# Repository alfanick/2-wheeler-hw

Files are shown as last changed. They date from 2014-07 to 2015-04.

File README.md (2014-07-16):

# TwoWheeler
TwoWheeler is Self Balancing Robot implemented using [XMOS startKIT](http://www.xmos.com/startkit) platform.

The robot is solving physical problem of inverted pendulum using PID regulator connecting motors with accelerometer. However its hardware design has much more features:
* 8 core 32-bit microcontroller
* bluetooth transceiver
* two distance meters
* motor driver with current sensing
* buck converter designed for use with LiPo battery
* battery voltage monitoring
* Over-The-Air parameters programming to built-in flash
* high torque motors with encoders

## Parts

* XMOS firmware - more in [balancer README](sw_twowheeler/app_balancer/README.md)
* computer app - API available in Ruby and console command interface with scripting (more in [documentation](ruby_twowheeler/README.md))
* circuit schematic and PCB design
* hardware design - not yet documented

## Authors

* Amadeusz Juskowiak - amadeusz@me.com
* Piotr Żurkowski  - kareth92@gmail.com

Inspired by Embedded Systems course at Poznan University of
Technology.

## License

*Copyright 2014 Amadeusz Juskowiak*

Licensed under the Apache License, Version 2.0 (the "License");
you may not use this file except in compliance with the License.
You may obtain a copy of the License at http://www.apache.org/licenses/LICENSE-2.0

Unless required by applicable law or agreed to in writing, software
distributed under the License is distributed on an "AS IS" BASIS,
WITHOUT WARRANTIES OR CONDITIONS OF ANY KIND, either express or implied.
See the License for the specific language governing permissions and
limitations under the License.

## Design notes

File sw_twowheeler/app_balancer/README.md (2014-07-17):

# TwoWheeler

## Commands

This is glossary of commands accepted and returned by TwoWheeler.
Every command must be ended with carriage return character to be
read.

### Requests

| Command | Description |
| --- | --- |
| FLASH | next cmd will use flash memory |
| FLASH=k | next k-cmds will use flash |
| V? | get battery voltage |
| PID? | get current PID coefficients |
| PID=p,i,d | set PID coefficients |
| PIDLP? | get current PID lowpass coeff  |
| PIDLP=a | set PID lowpass coefficient |
| RPM? | get RPM of motors |
| T? | get target angle |
| T=a | set target angle |
| T | set current angle as target |
| A? | get current pitch angle |
| ALP? | get current low pass coeff |
| ALP=a | set angle low pass coefficient |
| C? | get motors current |
| S | starts balancing |
| X | stop balancing |
| VER? | get firmware version |
| LOOPTIME? | get last loop execution time |
| LOOPDELAY?  | get loop delay |
| LOOPDELAY=t | set loop delay |
| SB? | get speed boost |
| SB=a | set speed boost |
| ST? | get speed threshold |
| ST=a | set speed threshold |

#### FLASH command

Lorem ipsum

### Replies

| Command | Description |
| --- | --- |
| OK | default command acknowledge |
| ERROR | malformed command |
| V=n | battery voltage in mV |
| PID=p,i,d | current PID coefficients |
| PIDLP=a | current PID lowpass coefficient|
| RPM=l,r | current motor RPM |
| C=l,r | motors current |
| T=a | current target angle |
| A=a | current pitch angle |
| ALP=a | current angle low pass coeff |
| VER=v | firmware git commit id |
| LOOPTIME=v  | last loop execution time in ms |
| LOOPDELAY=t | current loop delay in ms |
| SB=a | current speed boost |
| ST=a | current speed threshold |

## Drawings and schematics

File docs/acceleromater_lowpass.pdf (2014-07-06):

## Implemented on XMOS (angle lowpass=0.02, vector median=3)

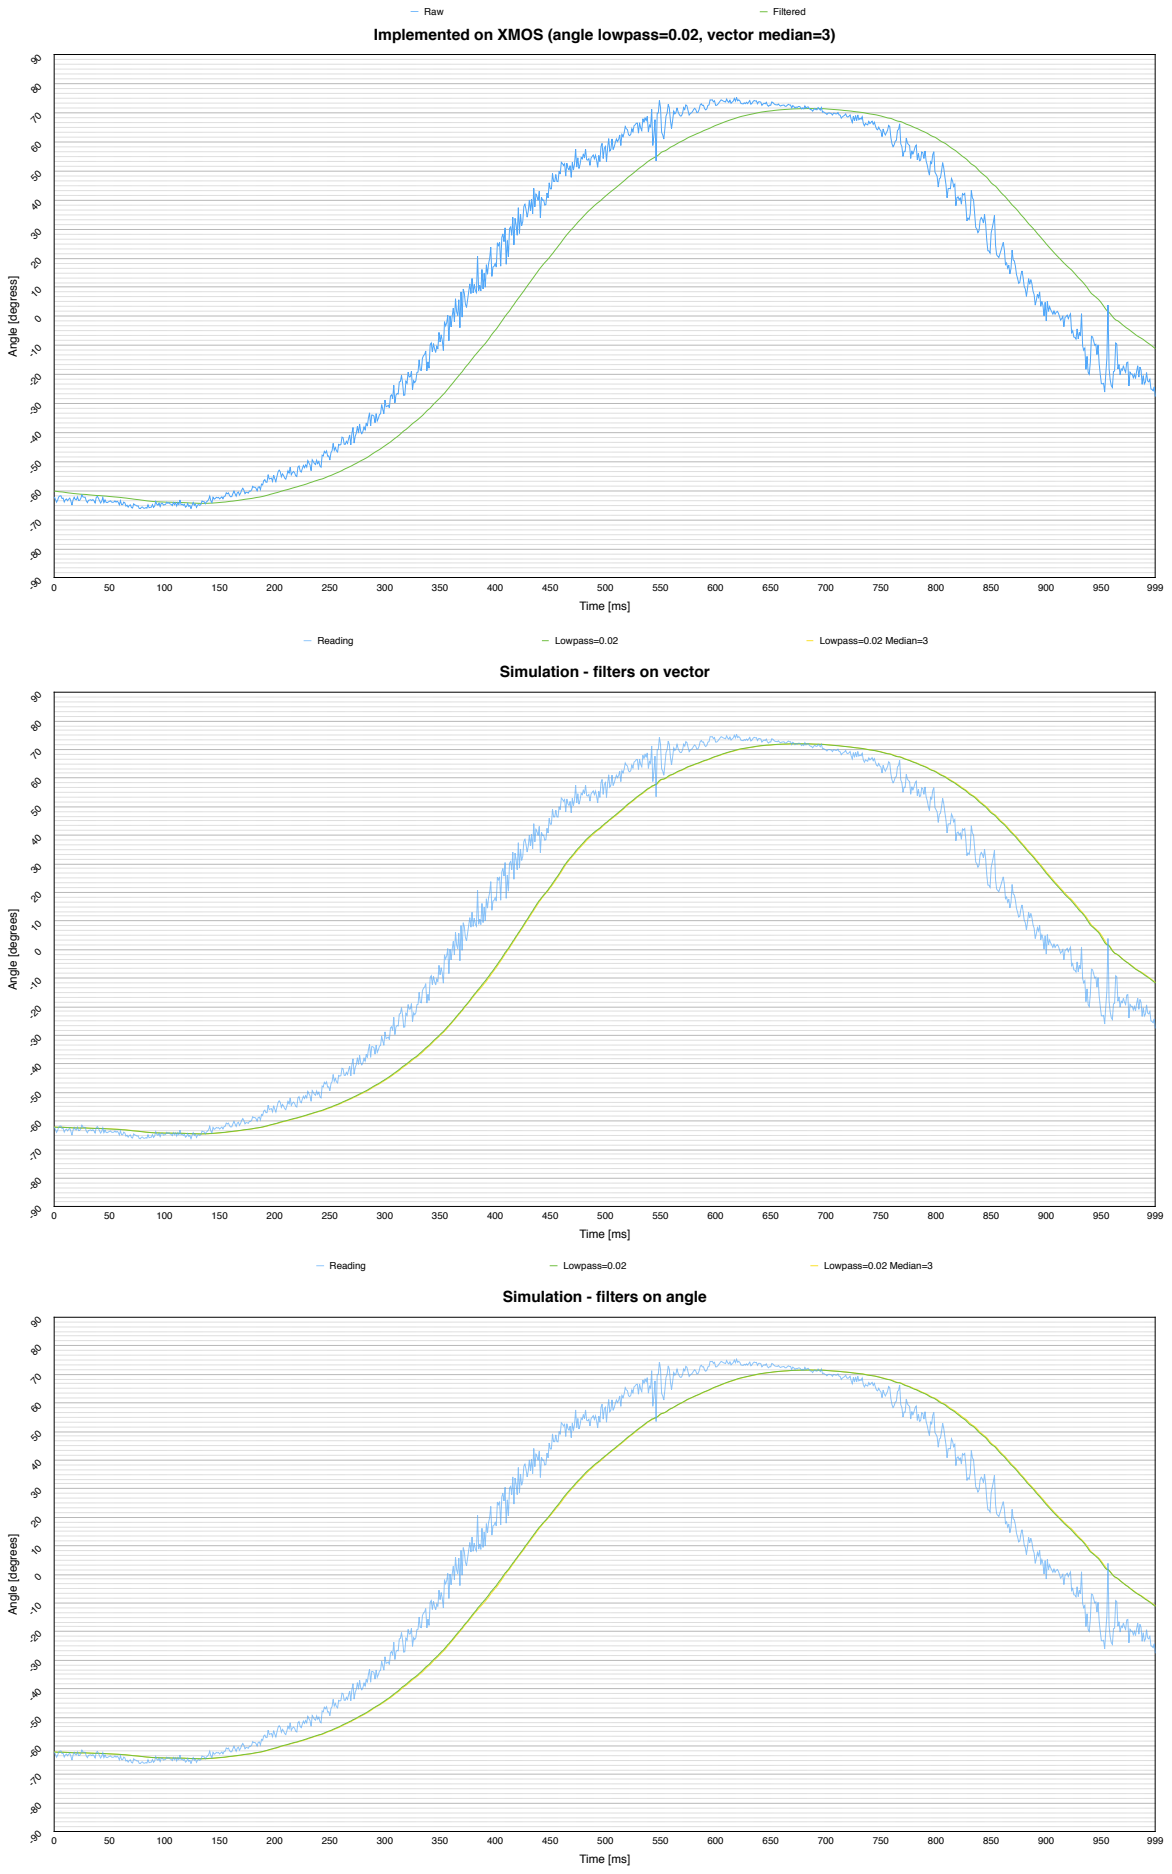
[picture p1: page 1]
Angle [degrees]; Time [ms]; Reading; Lowpass=0.02; Lowpass=0.02 Median=3; Angle [degress]; Raw; Filtered

Simulation - filters on vector

Simulation - filters on angle

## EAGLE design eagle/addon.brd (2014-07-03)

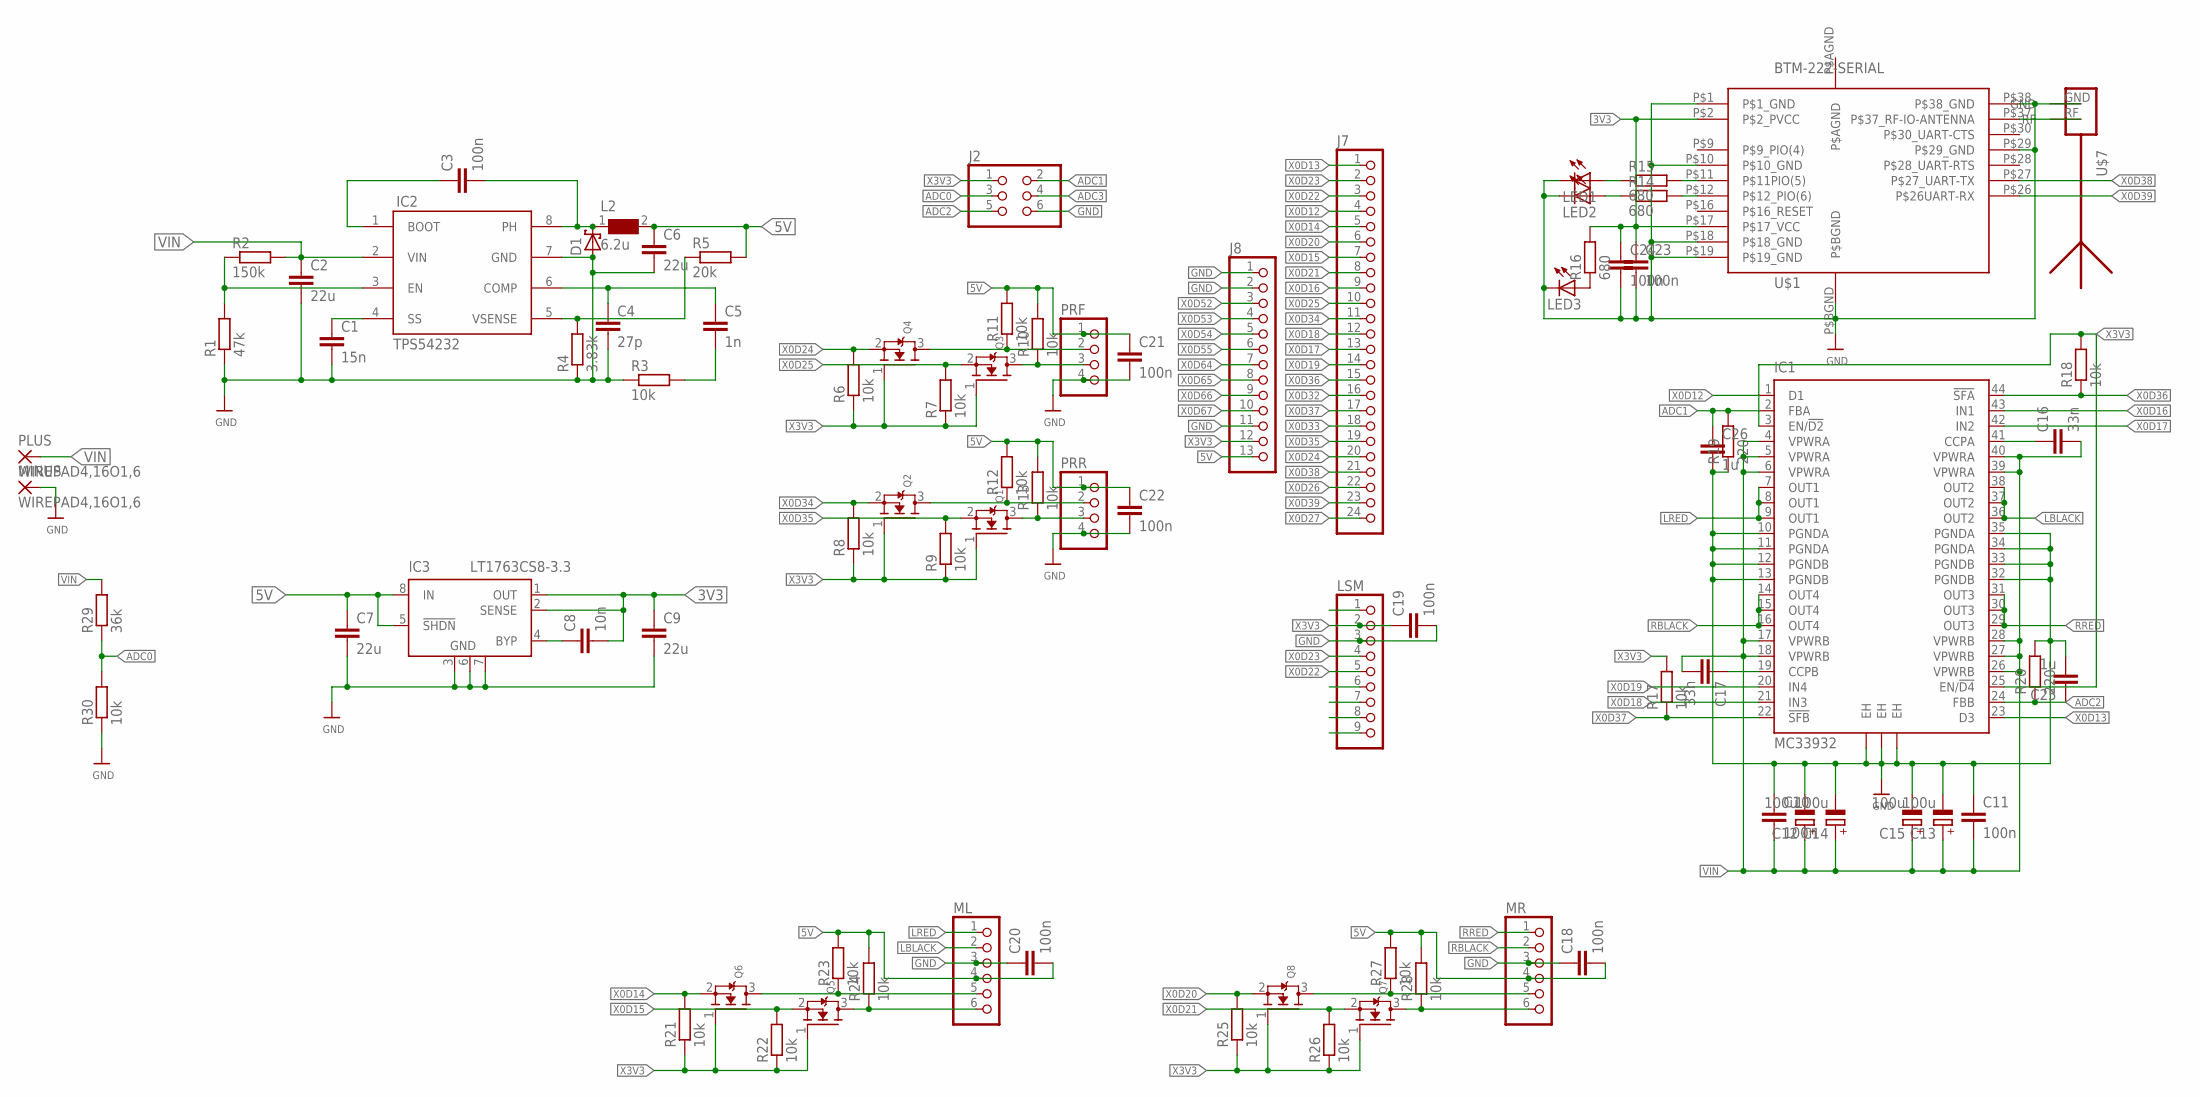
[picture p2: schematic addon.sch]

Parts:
C1: 15n; C0603
C2: 22u; C1210
C3, C10, C11, C18, C19, C20, C21, C22, C23, C24: 100n; C0603
C4: 27p; C0603
C5: 1n; C0603
C6: 22u; C1206
C7, C9: 22u; C0603
C8: 10n; C0603
C12, C13, C14, C15: 100u; D/7343-31R
C16, C17: 33n; C0603
C25, C26: 1u; C0603
D1: SCHOTTKY-DIODESMD; SMB
IC1: MC33932; HSOP44
IC2: TPS54232; YOURITRONICS_SO8
IC3: LT1763CS8-3.3; SOIC8
J2: PINHD-2X3; 2X03
J7: PINHD-1X24; 1X24
J8: PINHD-1X13; 1X13
L2: 6.2u; EAGLELIBRARY_WUERTH_ELEKTRONIK_EISOS_VERSION_6_WE-TPC_6823
LED1, LED2, LED3: LEDCHIPLED_0603; CHIPLED_0603
LSM: PINHD-1X9; 1X09
MINUS: WIREPAD4,16O1,6; 4,16O1,6
ML: PINHD-1X6; 1X06
MR: PINHD-1X6; 1X06
PLUS: WIREPAD4,16O1,6; 4,16O1,6
PRF: PINHD-1X4; 1X04
PRR: PINHD-1X4; 1X04
Q1, Q2, Q3, Q4, Q5, Q6, Q7, Q8: MOSFET-NREFLOW; SOT23-R
R1: 47k; R0603
R2: 150k; R0603
R3, R6, R7, R8, R9, R10, R11, R12, R13, R17, R18, R21, R22, R23, R24, R25, R26, R27, R28, R30: 10k; R0603
R4: 3.83k; R0603
R5: 20k; R0603
R14, R15, R16: 680; R0603
R19, R20: 220; R0603
R29: 36k; R0603
U$1: BTM-222-SERIAL; BTM-222
U$7: ANTENNA_1RIGHT; SWRA117D_RIGHT

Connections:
3V3: C8.2, C9.1, C23.1, C24.1, IC3.1 (OUT), IC3.2 (SENSE), R16.2, U$1.P$2 (P$2_PVCC), U$1.P$17 (P$17_VCC)
5V: C6.1, C7.1, C18.2, C20.2, C21.1, C22.1, IC3.5 (!SHDN), IC3.8 (IN), J8.13, L2.2, ML.4, MR.4, PRF.1, PRR.1, R5.2, R10.2, R11.2, R12.2, R13.2, R23.2, R24.2, R27.2, R28.2
ADC0: J2.3, R29.1, R30.2
ADC1: C26.1, IC1.2 (FBA), J2.2, R19.2
ADC2: C25.1, IC1.24 (FBB), J2.5, R20.1
ADC3: J2.4
GND: C1.2, C2.2, C4.2, C6.2, C7.2, C9.2, C10.1, C11.1, C12.-, C13.-, C14.-, C15.-, C18.1, C19.2, C20.1, C21.2, C22.2, C23.2, C24.2, C25.2, C26.2, D1.A, IC1.10 (PGNDA), IC1.11 (PGNDA), IC1.12 (PGNDB), IC1.13 (PGNDB), IC1.32 (PGNDB), IC1.33 (PGNDB), IC1.34 (PGNDA), IC1.35 (PGNDA), IC1.EH@1 (EH), IC1.EH@2 (EH), IC1.EH@3 (EH), IC2.7 (GND), IC3.3 (GND), IC3.6 (GND), IC3.7 (GND), J2.6, J8.1, J8.2, J8.11, LED1.C, LED2.C, LED3.C, LSM.3, MINUS.1, ML.3, MR.3, PRF.4, PRR.4, R1.1, R3.1, R4.1, R19.1, R20.2, R30.1, U$1.P$1 (P$1_GND), U$1.P$10 (P$10_GND), U$1.P$18 (P$18_GND), U$1.P$19 (P$19_GND), U$1.P$29 (P$29_GND), U$1.P$38 (P$38_GND), U$1.P$BGND, U$7.GND
LBLACK: IC1.36 (OUT2), IC1.37 (OUT2), IC1.38 (OUT2), ML.2
LRED: IC1.7 (OUT1), IC1.8 (OUT1), IC1.9 (OUT1), ML.1
unnamed: IC2.3 (EN), R1.2, R2.1
unnamed: C8.1, IC3.4 (BYP)
unnamed: PRR.3, Q1.3 (D), R13.1
unnamed: C3.1, IC2.1 (BOOT)
unnamed: C3.2, D1.C, IC2.8 (PH), L2.1
unnamed: C1.1, IC2.4 (SS)
unnamed: PRR.2, Q2.3 (D), R12.1
unnamed: C4.1, C5.1, IC2.6 (COMP)
unnamed: PRF.3, Q3.3 (D), R10.1
unnamed: C5.2, R3.2
unnamed: IC2.5 (VSENSE), R4.2, R5.1
unnamed: PRF.2, Q4.3 (D), R11.1
unnamed: U$1.P$37 (P$37_RF-IO-ANTENNA), U$7.RF
unnamed: R15.2, U$1.P$11 (P$11PIO(5))
unnamed: R14.2, U$1.P$12 (P$12_PIO(6))
unnamed: LED1.A, R15.1
unnamed: LED2.A, R14.1
unnamed: LED3.A, R16.1
unnamed: C16.1, IC1.41 (CCPA)
unnamed: C17.1, IC1.19 (CCPB)
unnamed: ML.6, Q5.3 (D), R24.1
unnamed: ML.5, Q6.3 (D), R23.1
unnamed: MR.6, Q7.3 (D), R28.1
unnamed: MR.5, Q8.3 (D), R27.1
P$AGND: U$1.P$AGND
RBLACK: IC1.14 (OUT4), IC1.15 (OUT4), IC1.16 (OUT4), MR.2
RRED: IC1.29 (OUT3), IC1.30 (OUT3), IC1.31 (OUT3), MR.1
VIN: C2.1, C10.2, C11.2, C12.+, C13.+, C14.+, C15.+, C16.2, C17.2, IC1.4 (VPWRA), IC1.5 (VPWRA), IC1.6 (VPWRA), IC1.17 (VPWRB), IC1.18 (VPWRB), IC1.26 (VPWRB), IC1.27 (VPWRB), IC1.28 (VPWRB), IC1.39 (VPWRA), IC1.40 (VPWRA), IC2.2 (VIN), PLUS.1, R2.2, R29.2
X0D12: IC1.1 (D1), J7.4
X0D13: IC1.23 (D3), J7.1
X0D14: J7.5, Q6.2 (S), R21.2
X0D15: J7.7, Q5.2 (S), R22.2
X0D16: IC1.43 (IN1), J7.9
X0D17: IC1.42 (IN2), J7.13
X0D18: IC1.21 (IN3), J7.12
X0D19: IC1.20 (IN4), J7.14
X0D20: J7.6, Q8.2 (S), R25.2
X0D21: J7.8, Q7.2 (S), R26.2
X0D22: J7.3, LSM.5
X0D23: J7.2, LSM.4
X0D24: J7.20, Q4.2 (S), R6.2
X0D25: J7.10, Q3.2 (S), R7.2
X0D26: J7.22
X0D27: J7.24
X0D32: J7.16
X0D33: J7.18
X0D34: J7.11, Q2.2 (S), R8.2
X0D35: J7.19, Q1.2 (S), R9.2
X0D36: IC1.44 (!SFA), J7.15, R18.1
X0D37: IC1.22 (!SFB), J7.17, R17.1
X0D38: J7.21, U$1.P$27 (P$27_UART-TX)
X0D39: J7.23, U$1.P$26 (P$26UART-RX)
X0D52: J8.3
X0D53: J8.4
X0D54: J8.5
X0D55: J8.6
X0D64: J8.7
X0D65: J8.8
X0D66: J8.9
X0D67: J8.10
X3V3: C19.1, IC1.3 (EN/!D2), IC1.25 (EN/!D4), J2.1, J8.12, LSM.2, Q1.1 (G), Q2.1 (G), Q3.1 (G), Q4.1 (G), Q5.1 (G), Q6.1 (G), Q7.1 (G), Q8.1 (G), R6.1, R7.1, R8.1, R9.1, R17.2, R18.2, R21.1, R22.1, R25.1, R26.1

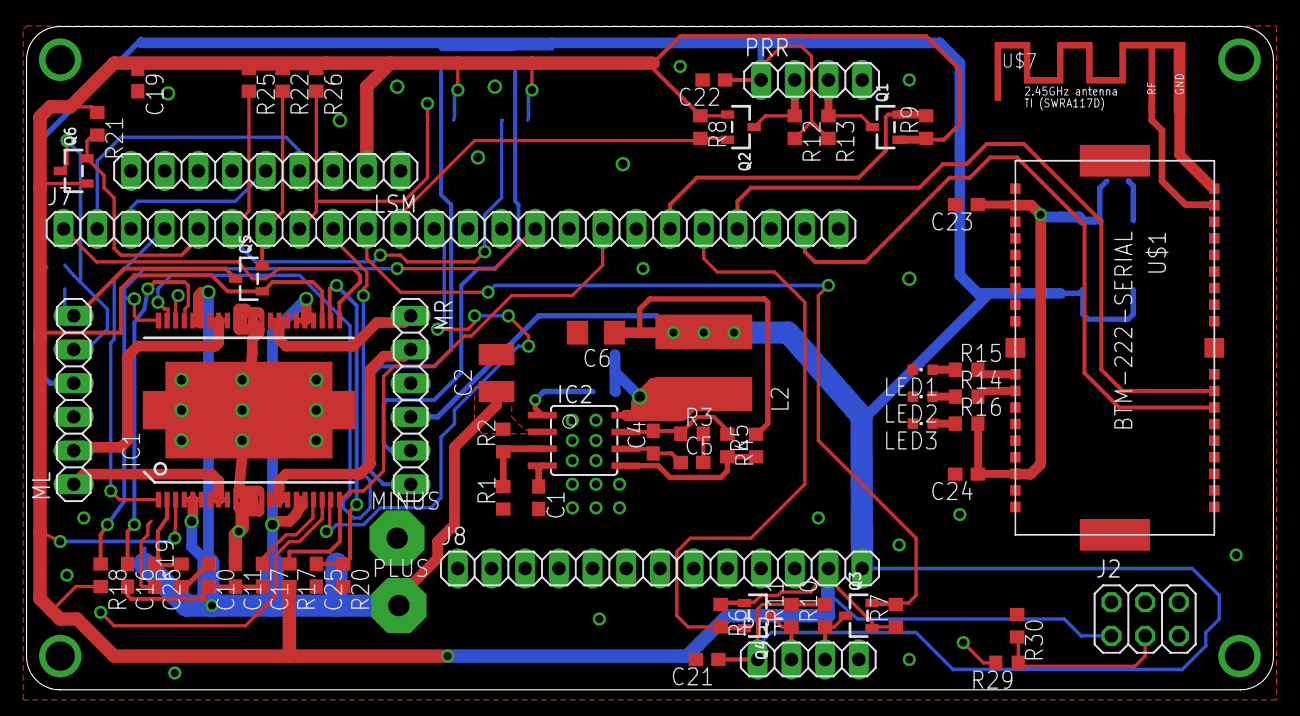
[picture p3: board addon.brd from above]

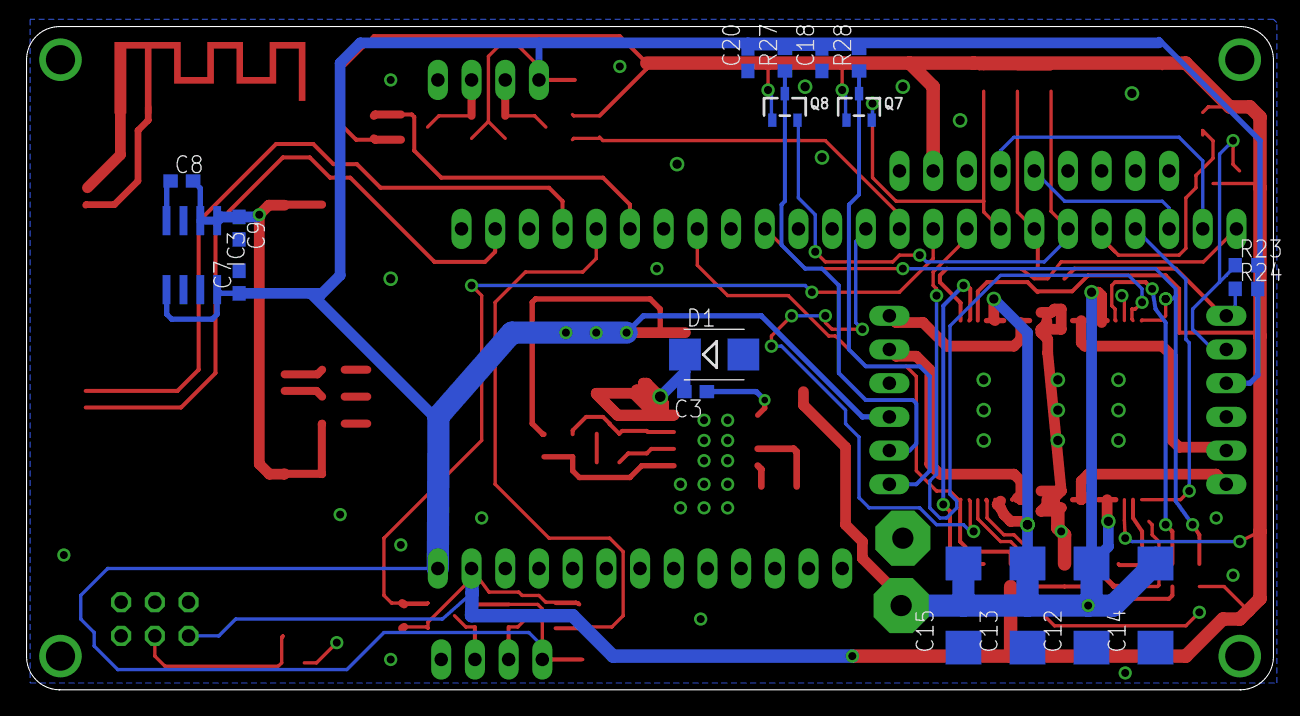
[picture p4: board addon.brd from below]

Board: 2 copper layers, 94.0 x 50.0 mm, 84 parts (18 on the bottom side), 56 nets.

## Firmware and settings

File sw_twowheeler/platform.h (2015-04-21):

#ifndef TWO_WHEELER_PLATFORM_H_
#define TWO_WHEELER_PLATFORM_H_

#define   FRONT_DISTANCE_SENSOR_TRIGGER            XS1_PORT_1I
#define      FRONT_DISTANCE_SENSOR_ECHO            XS1_PORT_1J

#define    REAR_DISTANCE_SENSOR_TRIGGER            XS1_PORT_1K
#define       REAR_DISTANCE_SENSOR_ECHO            XS1_PORT_1L

#define             MOTION_SENSOR_CLOCK            XS1_PORT_1G
#define              MOTION_SENSOR_DATA            XS1_PORT_1H

#define              BLUETOOTH_TRANSMIT            XS1_PORT_1P
#define               BLUETOOTH_RECEIVE            XS1_PORT_1O

#define              LEFT_MOTOR_DISABLE            XS1_PORT_1E
#define               LEFT_MOTOR_STATUS            XS1_PORT_1M

#define             RIGHT_MOTOR_DISABLE            XS1_PORT_1F
#define              RIGHT_MOTOR_STATUS            XS1_PORT_1N

#define               MOTORS_DIRECTIONS            XS1_PORT_4D
#define                  MOTORS_SENSORS            XS1_PORT_4C

#include <platform.h>
#include <xs1.h>

#include <uart_fast_tx.h>
#include <uart_fast_rx.h>
#include <distance_sensor.h>
#include <imu10.h>
#include <motors.h>

distance_sensor_t distance_sensors[2] = {
  { FRONT_DISTANCE_SENSOR_TRIGGER, FRONT_DISTANCE_SENSOR_ECHO },
  {  REAR_DISTANCE_SENSOR_TRIGGER,  REAR_DISTANCE_SENSOR_ECHO }
};

imu10_t motion_sensor = {
  MOTION_SENSOR_CLOCK,
  MOTION_SENSOR_DATA,
  250
};

motors_t motors_bridge = {
  {  LEFT_MOTOR_DISABLE,   LEFT_MOTOR_STATUS },
  { RIGHT_MOTOR_DISABLE,  RIGHT_MOTOR_STATUS },
  MOTORS_DIRECTIONS,
  MOTORS_SENSORS
};

in port bluetooth_receive = BLUETOOTH_RECEIVE;
out port bluetooth_transmit = BLUETOOTH_TRANSMIT;
const clock serial_clock = XS1_CLKBLK_REF;



#endif

/* vim: set ft=xc: */

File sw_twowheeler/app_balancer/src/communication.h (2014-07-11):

#ifndef APP_BALANCER_COMMUNICATION_H_
#define APP_BALANCER_COMMUNICATION_H_

#include <config.h>
#include "balancer.h"
#include "bluetooth.h"
#include "safety.h"


enum config_properties {
  config_balancer_speed_boost = 0, //++
  config_balancer_speed_threshold = 1, //++
  config_balancer_target = 2, //++
  config_balancer_pid = 3, //++
  config_balancer_pid_lowpass = 6,//++
  config_balancer_lowpass = 7,//++
  config_balancer_loop_delay = 8,//++
  EOF = 9
};


void parse_numbers(unsigned char where[], int length, int offset, int numbers[], const static int size);

[[combinable]]
void balancer_communication(balancer_client balancer, bluetooth_client bluetooth, balancer_sensors_client sensors);

#endif

/* vim: set ft=xc: */

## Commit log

2014-04-08 added template, added multithreaded led blinker
2014-04-09 added basic structure for pwm dc motor
2014-04-09 working PWM dc motor control
2014-04-09 combining motor tasks
2014-04-09 switching motor speed to check if pwm is implemented properly - everything is ok, yay
2014-04-10 moved motors to module
2014-04-10 moved distance sensor as module
2014-04-10 probably working distance sensor module - with variable frequency
2014-04-10 guarding timer if freq is 0, moved calculation to read
2014-04-11 testing SPI
2014-04-11 trying to use built-in spi
2014-04-11 moved to i2c protocol, working accmag readings, no api
2014-04-11 printing output
2014-04-13 made combnable, simple median filter
2014-06-19 added bluetooth pins, probably wrong tx/rx
    [platform.h]
2014-06-19 moved sensor structs to platform.h
2014-06-19 added board revision guards
2014-06-20 added motors
2014-06-20 added adc, not workign
2014-06-20 working adc
2014-06-20 added rx/tx uart, bluetooth testing
2014-06-24 motors movement
2014-06-24 higher freq, emergency cut off
2014-06-25 increased pwm resolution, experimenting with pid
2014-07-01 testing hall
2014-07-01 added motors status observing
2014-07-02 added current sensing
2014-07-02 playing with pid consts
2014-07-02 calibrated battery indicator, uart setup
2014-07-02 senidng battery voltage over bluetooth
2014-07-03 makefile for flashing without debug and scope, pid via bluetooth, commands, yay
2014-07-03 formal voltage output
2014-07-03 removed bug - not updating timer when breaking balancing
2014-07-03 added eagle files
    [addon.brd, addon.sch]
2014-07-03 added target calibration command
2014-07-04 Ki and Kd depandant on sample time
2014-07-04 changed pid coeffs to morelike balancing, made balancer.rb executable
2014-07-04 testing filters
2014-07-04 testing pwm freq
2014-07-04 clampign integral
2014-07-04 moved pid to function
2014-07-05 new pid, target
2014-07-05 1khz pwm freq
2014-07-05 removed filter - does not working, ggyro required, moved stopping when critical angle to safety;
2014-07-05 added simple lowpass filter to angle
2014-07-05 new pid coeefs
2014-07-06 moved lowpass and pitch to lsm
2014-07-06 new pid
2014-07-06 added alp command for lowpass filter parameter
2014-07-06 added lowpass filter setting based on delay
2014-07-06 added setting lowpass filter based on cutoff frequency, added aliases for self
2014-07-07 renamed sample time to loop delay, setting loop delay over the air
2014-07-07 added current reading
2014-07-07 added lowpass filters to current and battery adc
2014-07-07 more responsive current adc
2014-07-08 moved speed boost to pid, made speed threshold and boost accesible over bluetooth
2014-07-08 new synonyms and pid
2014-07-08 added sample gathering, lowpass on pid
2014-07-09 removed speed aliases - motors should be used, made synonyms of self readonly
2014-07-11 added adc lock mock
2014-07-11 spinoff of startkit adc
2014-07-11 working releasing and acquiring adc port for flash/adc - still need to do config_open
2014-07-16 redone unsafe pointers, working flash AND adc
2014-07-16 disabling adc completely
2015-04-21 using moving to imu module
2015-04-22 gyro test

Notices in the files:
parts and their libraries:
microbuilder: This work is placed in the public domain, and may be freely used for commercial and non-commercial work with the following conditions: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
